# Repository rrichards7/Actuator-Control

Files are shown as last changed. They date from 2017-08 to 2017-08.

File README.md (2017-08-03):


# Autonomous Snowmobile Linear Actuator Control #

*Lead Architect: Ryan J. Richards*

*The Pennsylvania State University - School of Electrical Engineering and Computer Science*

## Introduction/Methodology ##

The linear actuator is used to control the steering angle of the snowmobile. A motor shield (attached to the main ArduinoMEGA) serves as a programmable switch between the Arduino and the actuator. Although a relay would be the simplest way to control the actuator, the actuator must be constantly switched on/off and move in different directions. Switching a relay too often significantly lowers the lifespan of the device. However, by using a motor shield with the Arduino, **Pulse Width Modulation** (PWM) can be used - which can be constantly switched without worry *and* has the programmatical ability to reverse the polarity of the power supplied to the actuator (which gives makes it either *extend* or *retract*).

## MakerHub LINX ##

LINX is a library developed by MakerHub that allows programmers to interface with the RaspberryPi, Arduino and other microcontrollers on LabVIEW. LINX has been used extensively in this project to communicate with the ArduinoMEGA, which controls each subsystem. Download and other information can be found at:

[MakerHub LINX](http://sine.ni.com/nips/cds/view/p/lang/en/nid/212478)

## Hardware Setup ##

The actuator setup utilizes a motor shield [1] that attaches to the ArduinoMEGA. This shield is capable of controling two motors, however we will only need to control one. The motor shield has the following schematic:



*Setup instructions:*

(1) connect the **External Power Jack** to a power supply/battery with the appropriate voltage/current

(2) connect the **M1+** jack to the positive terminal of the actuator

(3) connect the **M1-** jack to the negative terminal of the actuator

(4) attach the **Motor Shield** to the ArduinoMEGA - ensuring that the setup matches the pictures below:





The final setup should look like this:



## LabVIEW Code ##

This LabVIEW code exemplifies the basic control system for the actuator using the motor shield. The code used in the SnowDrone main VI uses this setup but separates the configuration slightly to accomodate the message-based architecture.



*Setup and execution:*

(1) set the **PWM Channel** to **9**

(2) set the **IN1 Channel** to **8**

(3) set the **IN2 Channel** to **11**

(4) set the **Duty Cycle** to **1**

(5) set the **Serial Port** to the COM port of the ArduinoMEGA

(6) Run the VI and press either the **Extend** or **Retract** button - the actuator will then extend/retract accordingly

(7) Press the **Stop** button when done (rather than aborting execution - this ensures that the Arduino connection is closed)

ezgif com-video-to-gif 1


## Mounting to Snowmobile ##

Mounting the actuator to the snowmobile is a very laborious task since there are very few mounting points on the snowmobile itself. 

The 2015 PSU SnowDrone team sought to mount the actuator on a metal apparatus (which attached to the seat of the snowmobile) and connect the actuator to the steering handle itself. However, the steering handle did not move in a linear motion which means that this is not an optimal mounting position. 

The 2017 PSU SnowDrone team sought to mount the actuator to the bottom of the snowmobile - one end connecting to the front sled steering connection itself while the other end connects to some fixed point on the snowmobile. This proved to be a hard but (semi) achievable task.

Propsed connection steps:

(1) connect the moveable end of the actuator to the right-sled steering base



(2) connect the fixed end of the actuator to bolt openning on the base of the snowmobile



**Note:** The fixed-point mounting is highly susceptible to movement and is not entirely secure - therefore a mounting reinforcement piece must be designed. The piece must attach to a stable location/set of points and be large enough to extend to the mounting point of interest.

## Reinforced Fixed Point ##

Since the fixed point on the snowmobile was not a sturdy enough mounting position, a mounting bracket was designed in SolidWorks which reinforces the fixed point. The snowmobile's running board has secure holes where bolts can penetrate the metal and have a stable connection. The mounting bracket extends from the running board bolt holes to the actuator fixed point. The mounting bracket is thick and can be printed in tough PLA (plastic) - lightweight but still strong enough to support the actuator. The bracket has a specially designed hole which accomodates the actuator pin - a sturdy piece which goes into the actuator mounting hole (rather than using a thin screw), this is evidenced in the SolidWorks pictures below.

**Note:** All solidworks parts and the final mounting assembly can be downloaded from this GitHub repository.





 

## Future Considerations ##

(1) A new motor shield must be purchased since the power draw of the actuator is too large for the current motor shield and therefore will be severely limited in its pushing/pulling capabilities. The optimal choice for a new motor shield is: [Motor Controller](http://www.robotshop.com/en/cytron-13a-5-30v-single-dc-motor-controller.html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)

(2) New mounting point for fixed side of actuator that will be secure enough to withstand the force of the actuator. 

## Appendix ##

[1] [Motor shield information](http://wiki.seeedstudio.com/wiki/Motor_Shield_V1.0)

[2] [Linear Actuator Website](http://www.thomsonlinear.com/website/com/eng/products/actuators/electrak_2.php)

[3] [Linear Actuator manual](http://www.thomsonlinear.com/downloads/actuators/Electrak_2_Installation_Manual_mnen.pdf)

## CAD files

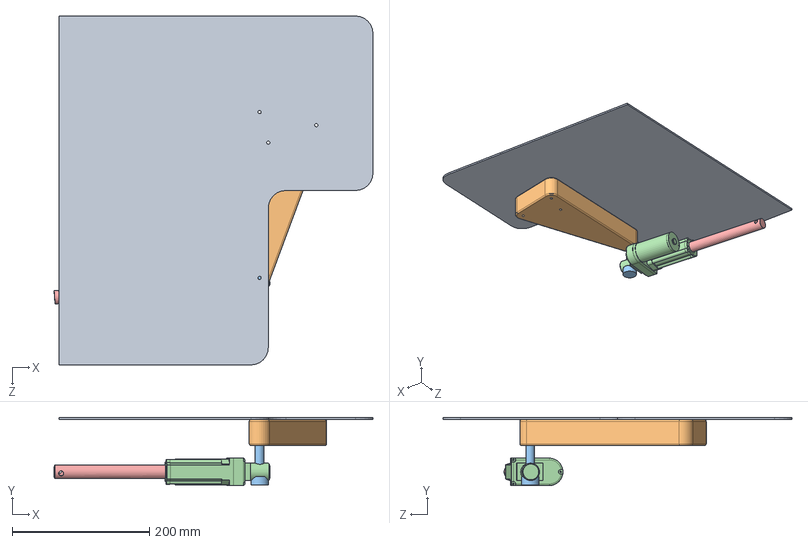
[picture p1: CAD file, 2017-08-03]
SolidWorks/MountingAssembly.SLDASM
464.4 x 99.4 x 508.0 mm
sheet metal
mountingBracket
actuatorPin
linear_actuator_2inch_stroke
shaft_2inches

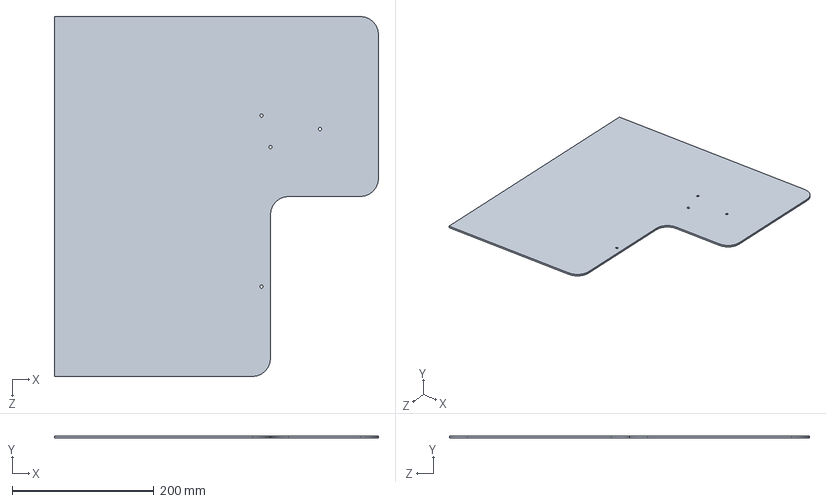
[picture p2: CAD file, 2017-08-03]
SolidWorks/sheet metal.SLDPRT
457.2 x 3.17 x 508.0 mm

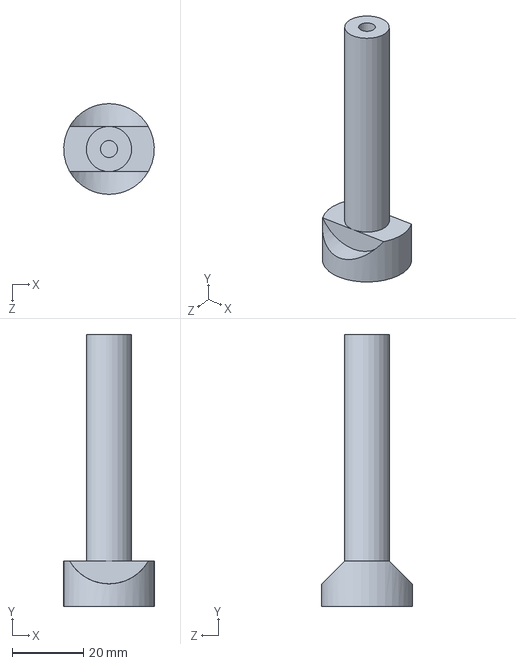
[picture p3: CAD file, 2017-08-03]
SolidWorks/actuatorPin.SLDPRT
25.4 x 76.2 x 25.4 mm

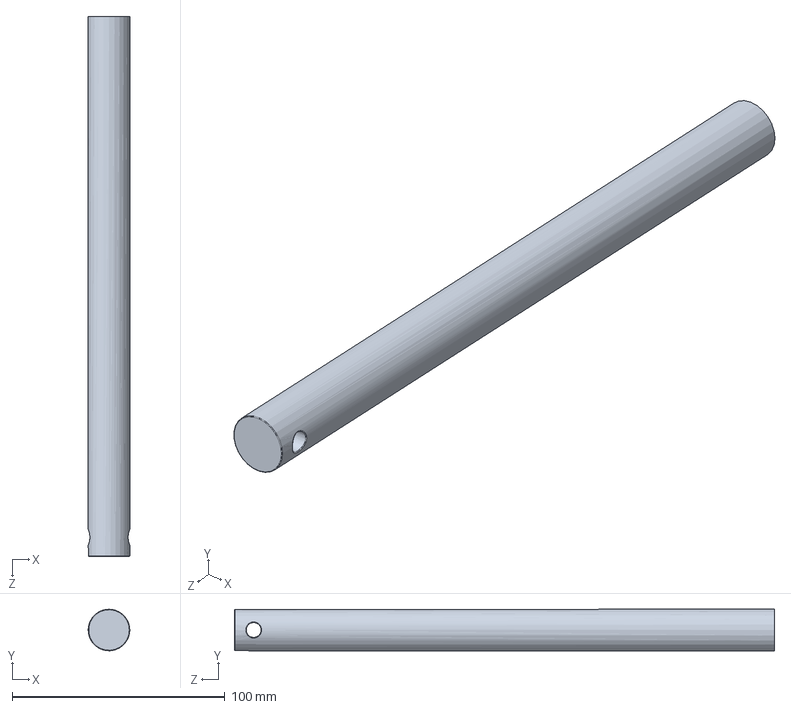
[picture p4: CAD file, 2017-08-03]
SolidWorks/shaft_2inches.sldprt
19.6 x 19.6 x 254.0 mm

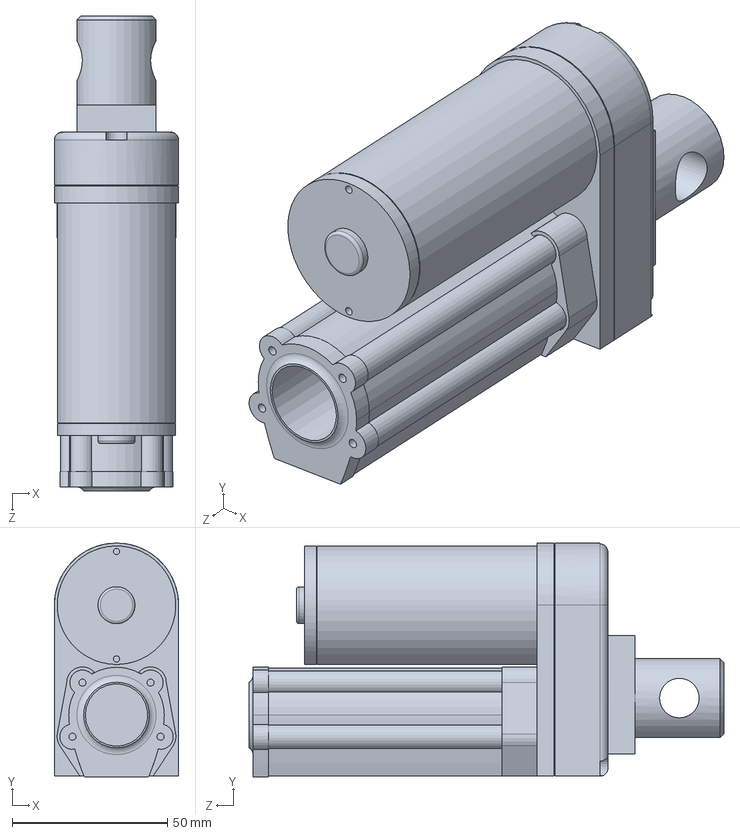
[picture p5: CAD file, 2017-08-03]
SolidWorks/linear_actuator_2inch_stroke.SLDPRT
40.0 x 75.3 x 152.8 mm

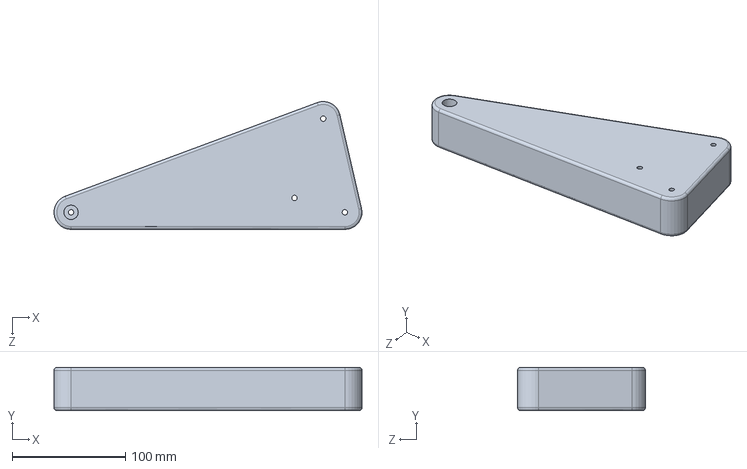
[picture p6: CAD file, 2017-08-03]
SolidWorks/mountingBracket.SLDPRT
271.4 x 38.1 x 112.7 mm
